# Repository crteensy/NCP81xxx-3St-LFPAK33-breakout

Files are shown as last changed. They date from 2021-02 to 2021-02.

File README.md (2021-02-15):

# NCP81xxx-3St-LFPAK33-breakout
Breakout board for gate drivers like NCP81253 or NCP81161 with 3-state PWM input and FETs in LFPAK33 like the PSMN1R8-30MLH

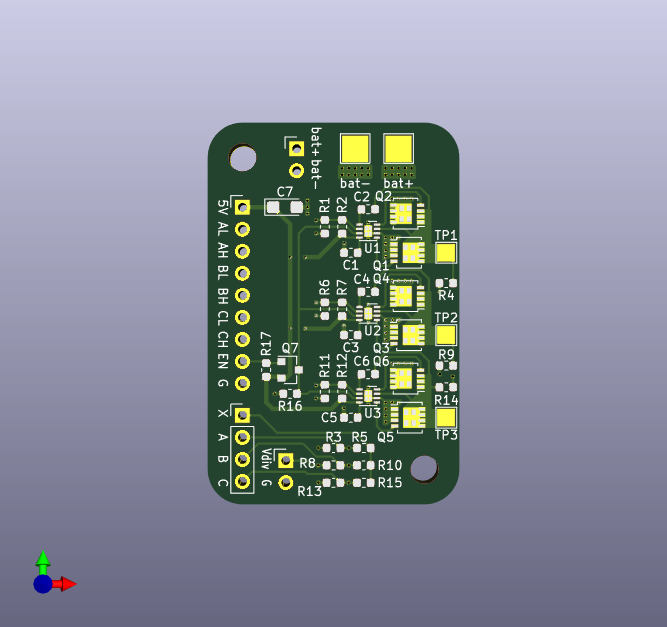
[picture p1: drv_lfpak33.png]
3D view


## Purpose
The purpose of this breakout board is to simplify BLDC ESC development by separating MCU and power stage on different boards. That way a proven gate driver/FET power stage can be used with different MCUs, or working code can be used with different power stages.

## Features
Inputs:
- active low enable for all gate drivers
- high side and low side inputs for each gate driver, wired to a pair of pull-up resistors to generate 3-state PWM with either) two plain open-drain outputs or) one plain open drain output for the low side and one resistive open drain output for the high side.

You can choose to connect the phase feedback voltage dividers to ground on J2 using a jumper or to bias them with an external voltage supply (1V2 has worked here). This feature was necessary to implement BLDC control with an ADC whose input range doesn't extend below ground (this was the case with PSoC6).

Outputs:
- Motor connections of course
- phase feedback voltage divider output.

## PCB design rules (if you want to get them made):
- Layers: 2
- smallest drill: 0.3 mm
- track width/spacing: 0.2 mm
so nothing special at all.

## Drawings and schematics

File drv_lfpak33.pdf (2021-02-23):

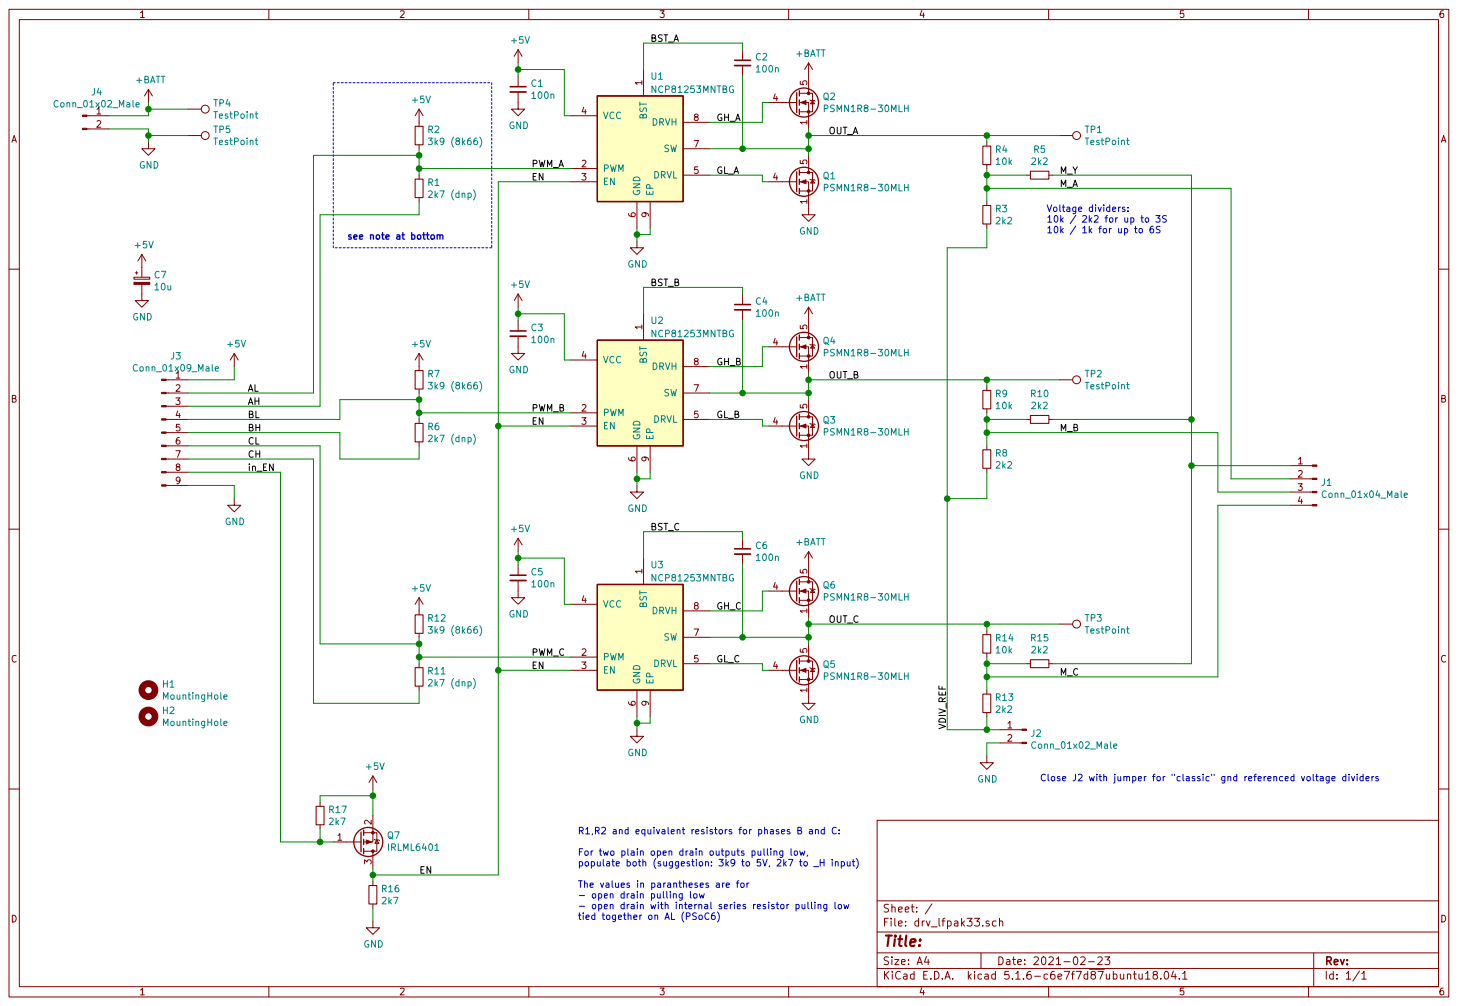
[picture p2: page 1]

1 PWM 2 EN 3 VCC 4 DRVL 5 GND

see note at bottom
H2MountingHole H1MountingHole GND

Close J2 with jumper for "classic" gnd referenced voltage dividers

R1,R2 and equivalent resistors for phases B and C:

For two plain open drain outputs pulling low,
populate both (suggestion: 3k9 to 5V, 2k7 to _H input)

The values in parantheses are for
- open drain pulling low
- open drain with internal series resistor pulling low
tied together on AL (PSoC6)

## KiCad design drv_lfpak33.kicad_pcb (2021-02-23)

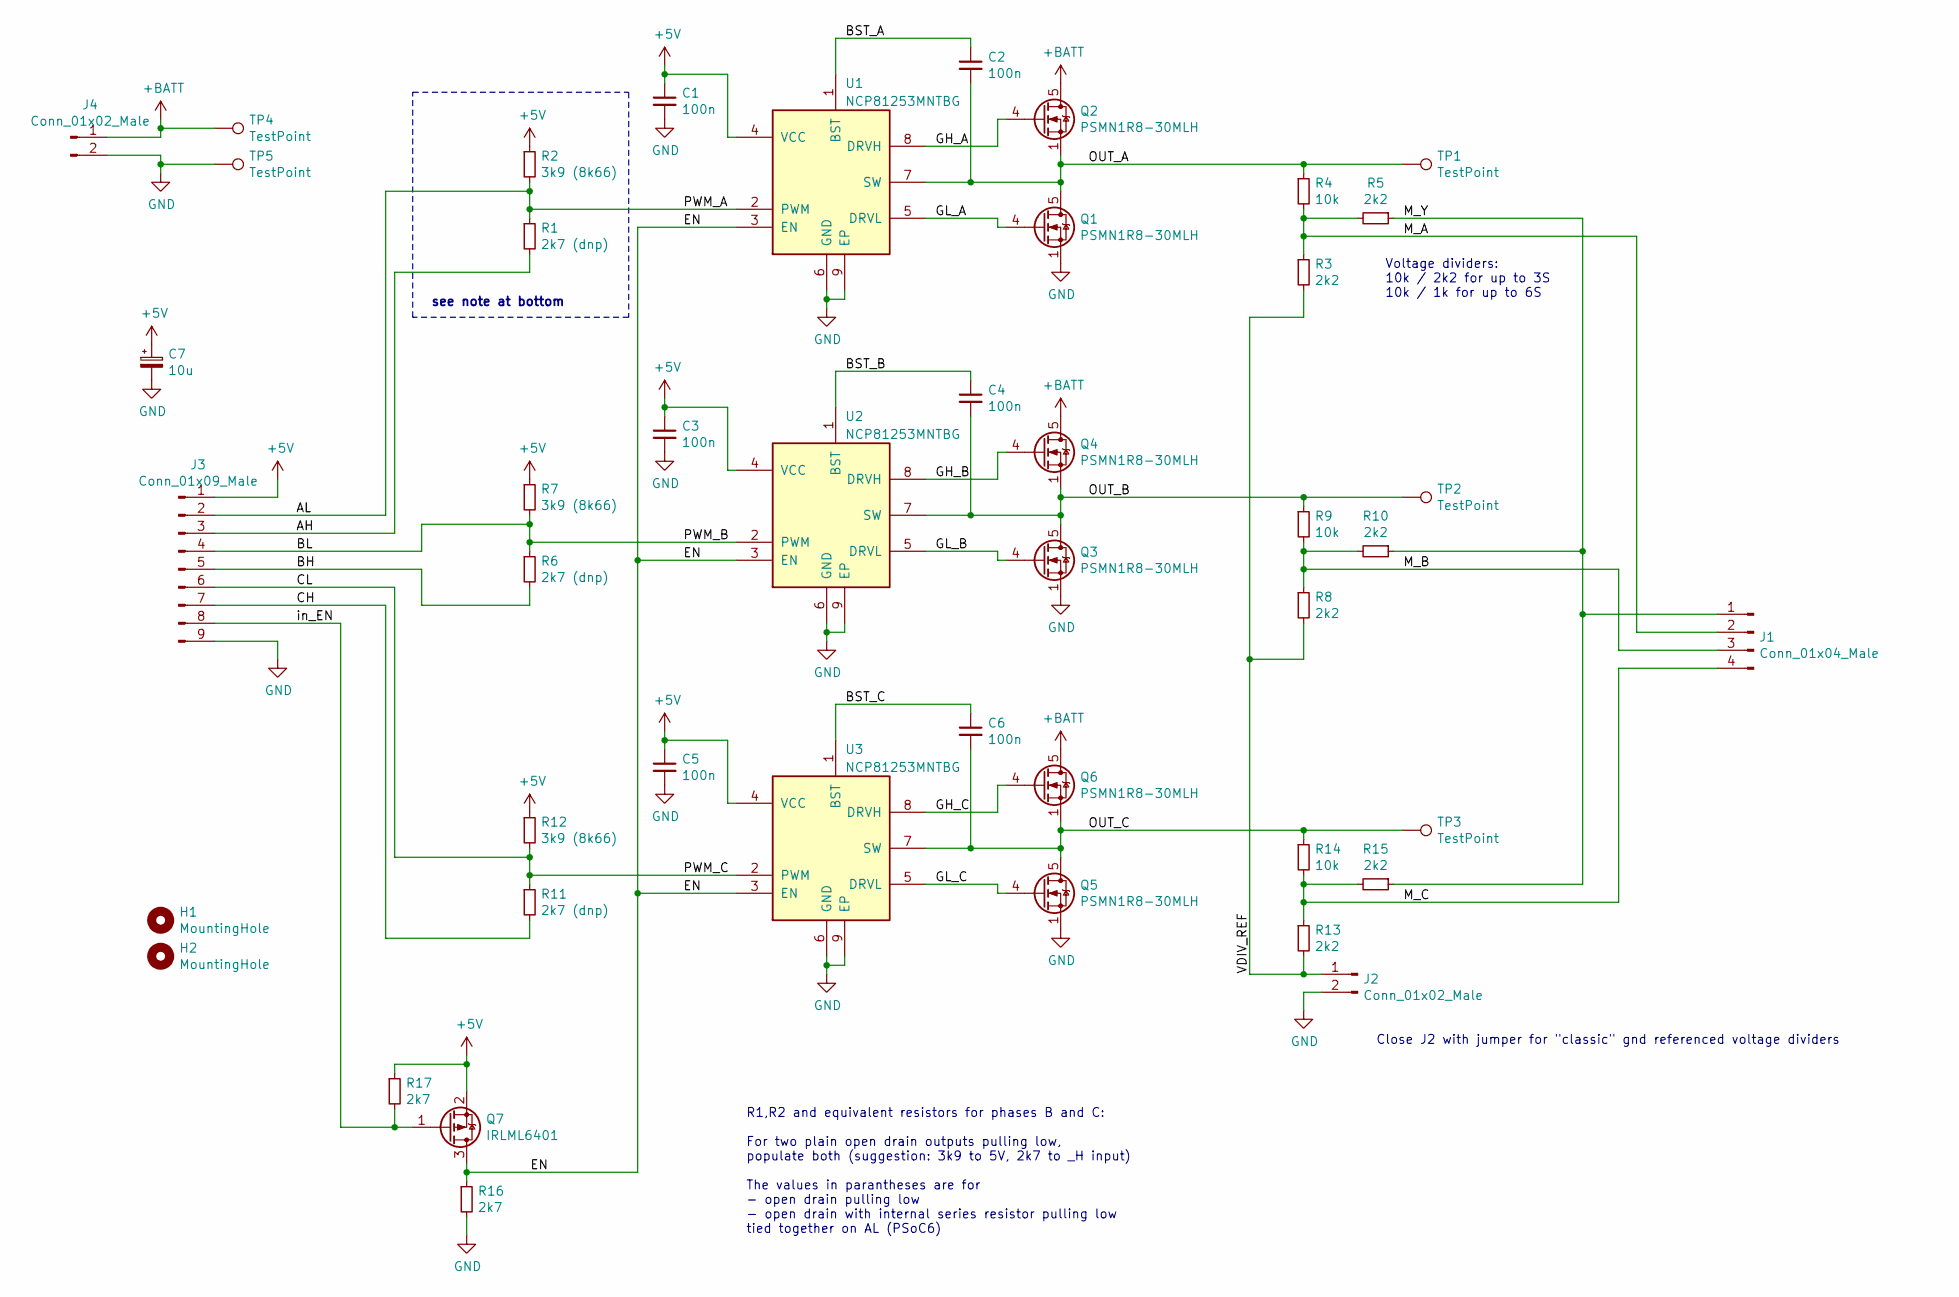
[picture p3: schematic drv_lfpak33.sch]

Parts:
C1, C2, C3, C4, C5, C6: 100n; C_0603_1608Metric
C7: 10u; CP_EIA-3216-18_Kemet-A
H1, H2: MountingHole; MountingHole_3.2mm_M3
J1: Conn_01x04_Male; PinHeader_1x04_P2.54mm_Vertical
J2, J4: Conn_01x02_Male; PinHeader_1x02_P2.54mm_Vertical
J3: Conn_01x09_Male; PinHeader_1x09_P2.54mm_Vertical
Q1, Q2, Q3, Q4, Q5, Q6: PSMN1R8-30MLH; LFPAK33
Q7: IRLML6401; SOT-23
R1, R6, R11: 2k7 (dnp); R_0603_1608Metric
R2, R7, R12: 3k9 (8k66); R_0603_1608Metric
R3, R5, R8, R10, R13, R15: 2k2; R_0603_1608Metric
R4, R9, R14: 10k; R_0603_1608Metric
R16, R17: 2k7; R_0603_1608Metric
TP1, TP2, TP3: TestPoint; TestPoint_Pad_2.0x2.0mm
TP4, TP5: TestPoint; TestPoint_Pad_3.0x3.0mm
U1, U2, U3: NCP81253MNTBG; DFN-8-1EP_2x2mm_P0.5mm_EP0.9x1.3mm

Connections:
+5V: C1.1, C3.1, C5.1, C7.1, J3.1, Q7.2 (S), R2.1, R7.1, R12.1, R17.1, U1.4 (VCC), U2.4 (VCC), U3.4 (VCC)
+BATT: J4.1, Q2.5 (D), Q4.5 (D), Q6.5 (D), TP4.1
/AH: J3.3, R1.2
/AL: J3.2, R1.1, R2.2, U1.2 (PWM)
/BH: J3.5, R6.2
/BL: J3.4, R6.1, R7.2, U2.2 (PWM)
/BST_A: C2.1, U1.1 (BST)
/BST_B: C4.1, U2.1 (BST)
/BST_C: C6.1, U3.1 (BST)
/CH: J3.7, R11.2
/CL: J3.6, R11.1, R12.2, U3.2 (PWM)
/EN: Q7.3 (D), R16.1, U1.3 (EN), U2.3 (EN), U3.3 (EN)
/GH_A: Q2.4 (G), U1.8 (DRVH)
/GH_B: Q4.4 (G), U2.8 (DRVH)
/GH_C: Q6.4 (G), U3.8 (DRVH)
/GL_A: Q1.4 (G), U1.5 (DRVL)
/GL_B: Q3.4 (G), U2.5 (DRVL)
/GL_C: Q5.4 (G), U3.5 (DRVL)
/M_A: J1.2, R3.1, R4.2, R5.2
/M_B: J1.3, R8.1, R9.2, R10.2
/M_C: J1.4, R13.1, R14.2, R15.2
/M_Y: J1.1, R5.1, R10.1, R15.1
/OUT_A: C2.2, Q1.5 (D), Q2.1 (S), Q2.2 (S), Q2.3 (S), R4.1, TP1.1, U1.7 (SW)
/OUT_B: C4.2, Q3.5 (D), Q4.1 (S), Q4.2 (S), Q4.3 (S), R9.1, TP2.1, U2.7 (SW)
/OUT_C: C6.2, Q5.5 (D), Q6.1 (S), Q6.2 (S), Q6.3 (S), R14.1, TP3.1, U3.7 (SW)
/VDIV_REF: J2.1, R3.2, R8.2, R13.2
/in_EN: J3.8, Q7.1 (G), R17.2
GND: C1.2, C3.2, C5.2, C7.2, J2.2, J3.9, J4.2, Q1.1 (S), Q1.2 (S), Q1.3 (S), Q3.1 (S), Q3.2 (S), Q3.3 (S), Q5.1 (S), Q5.2 (S), Q5.3 (S), R16.2, TP5.1, U1.6 (GND), U1.9 (EP), U2.6 (GND), U2.9 (EP), U3.6 (GND), U3.9 (EP)

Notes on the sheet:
see note at bottom
R1,R2 and equivalent resistors for phases B and C: For two plain open drain outputs pulling low, populate both (suggestion: 3k9 to 5V, 2k7 to _H input) The values in parantheses are for - open drain pulling low - open drain with internal series resistor pulling low tied together on AL (PSoC6)
Close J2 with jumper for "classic" gnd referenced voltage dividers
Voltage dividers: 10k / 2k2 for up to 3S 10k / 1k for up to 6S

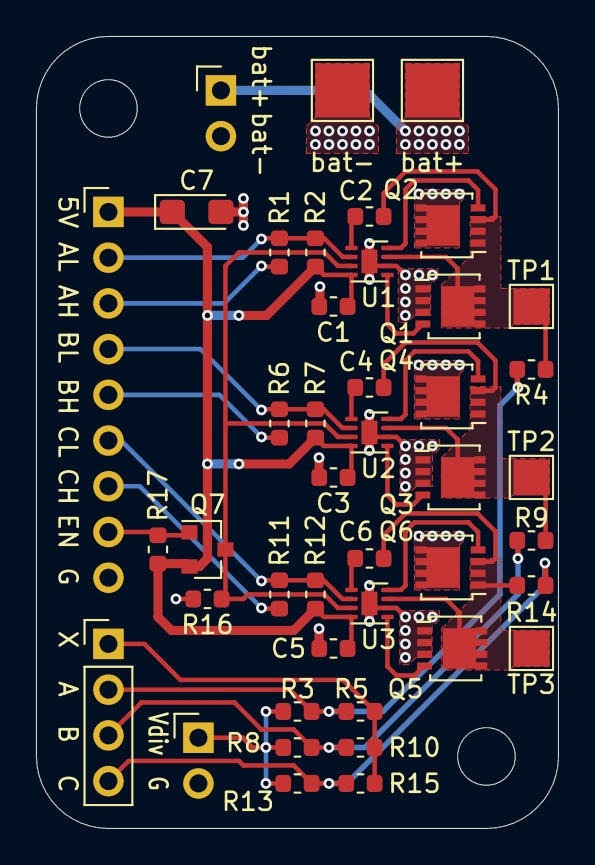
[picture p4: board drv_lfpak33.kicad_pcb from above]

Board: 2 copper layers, 29.0 x 44.0 mm, 45 parts (0 on the bottom side), 28 nets.

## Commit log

2021-01-28 initial kicad project commit
    [drv_lfpak33.kicad_pcb, drv_lfpak33.sch]
2021-02-13 update schematic: correct pull resistor values
    [drv_lfpak33.kicad_pcb, drv_lfpak33.sch]
2021-02-14 update bottom silkscreen
    [drv_lfpak33.kicad_pcb]
2021-02-23 add mounting holes
    [drv_lfpak33.kicad_pcb, drv_lfpak33.sch]
2021-02-23 update 3d view and schematic pdf
    [drv_lfpak33.kicad_pcb, drv_lfpak33.sch]
